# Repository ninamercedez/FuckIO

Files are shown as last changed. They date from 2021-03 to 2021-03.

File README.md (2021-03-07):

# FuckIO
An opensource fucking machine, that is far superiour to anything on the market.
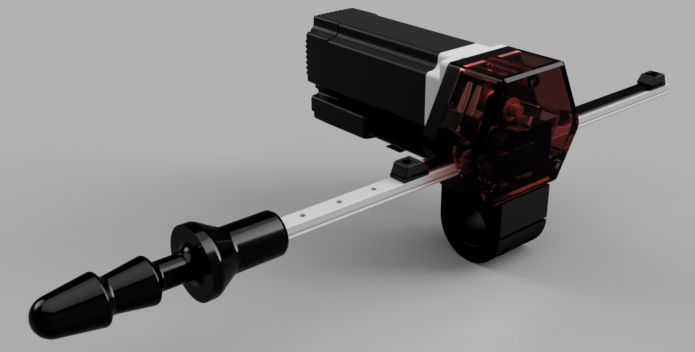
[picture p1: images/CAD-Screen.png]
Rendering


## Specs
* Easy to built just with a 3D-printer, screwdrivers and easy-to-source parts.
* Completely 3D-printable with easy to print parts and almost no supports. Also avoiding tight tolerances to make this accessable as possible. 
* Simple, yet verastile mechanics.
* Based on a linear position drive, not a crank mechanism.
* Double 24V PWM output to drive external systems. Could be lube pumps, vibrators, etc.

## Mechanics
The mechanics is a direct derivative of an other open source project called OSSM. You can also find some informations about this build on their Discord.
https://github.com/KinkyMakers/OSSM-hardware

The motor mount is designed for a NEMA23 servo or stepper motor. Any motor fitting to this standart should work. 

### BOM
* iHSV57-30-18-36-... integrated servo motor from JMC
* 24V Power Brick Mean Well GST280A24-C6P 
* 40cm MGN12H linear rail
* 4x 605-2RS Z2 bearings
* Micro Switch
* GT2 20 Tooth Pulley for 8mm Axis and a 10mm belt
* GT2 belt with 10mm width
* Various M3 and M5 screws and nuts
* Arduino Nano33 IoT

## Electronics
The electronics board is used to interface an external stepper or servo controller. I can't drive a motor directly. It is based around an Arduino Nano33 IoT to enable BLE or WiFi support. It sends 5V DIR, PUL, ENA signals and expects FAULT signal and a homing switch. Two MOSFETs with freewheeling diodes allow PWM control of external systems running of the 24V supply.

## Firmware
The firmware uses a self developed stepper library. It uses the SAMD21 timer perihperials to generate the PUL signal. That way it is possible to create a much higher step rate with no processor loading. Popular Arduino libraries like AccelStepper are not up to the task.

__Do not use this firmware! It is heavly beeing worked on. It will destroy your hardware!__

## Control Software
No control software yet. But it is planned to use node-red in combination with MQTT messages.

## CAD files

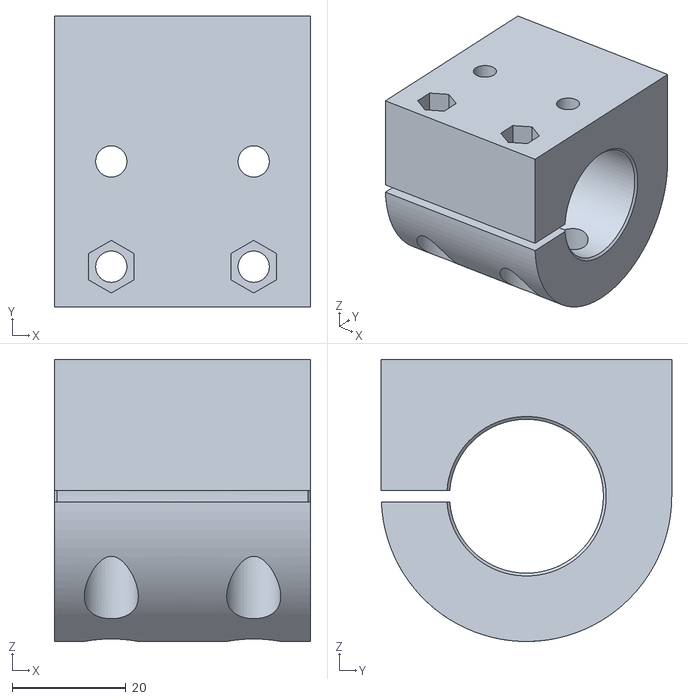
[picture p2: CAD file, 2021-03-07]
hardware/mechanics/3_4in Pipe Clamp.stl
45.0 x 51.0 x 49.5

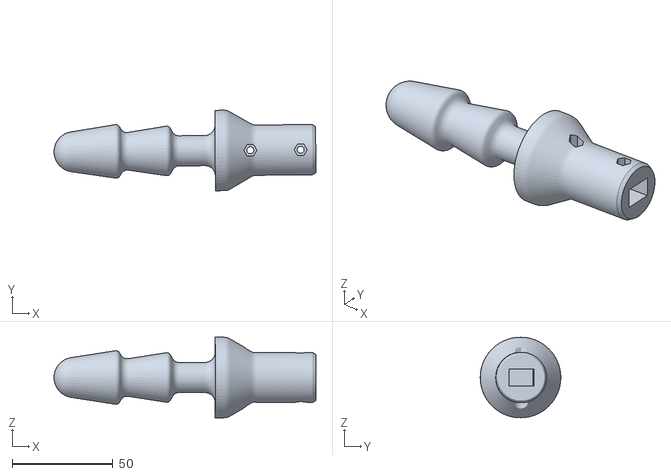
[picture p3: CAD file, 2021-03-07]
hardware/mechanics/Vac-u-Lock.stl
130.1 x 40.0 x 40.0

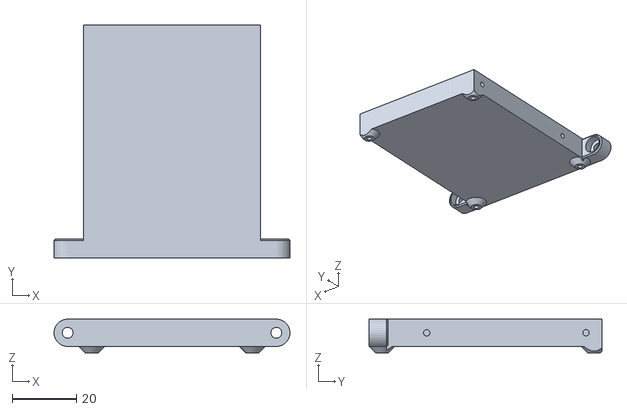
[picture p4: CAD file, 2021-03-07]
hardware/mechanics/PCB Holder.stl
73.5 x 72.6 x 10.5

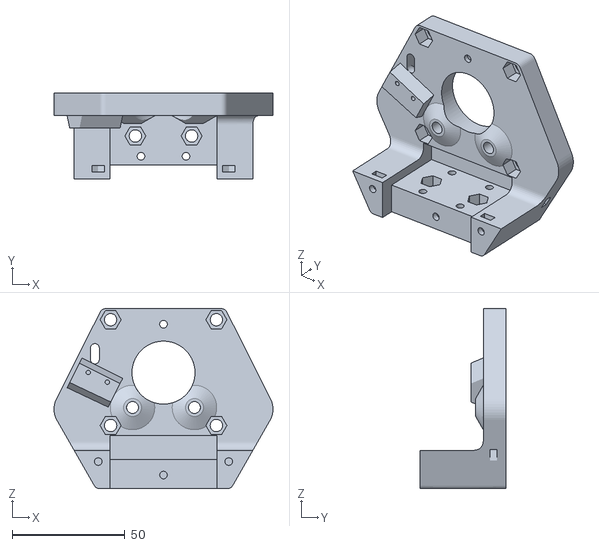
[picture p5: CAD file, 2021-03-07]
hardware/mechanics/Motor Mount.stl
97.3 x 38.0 x 80.0

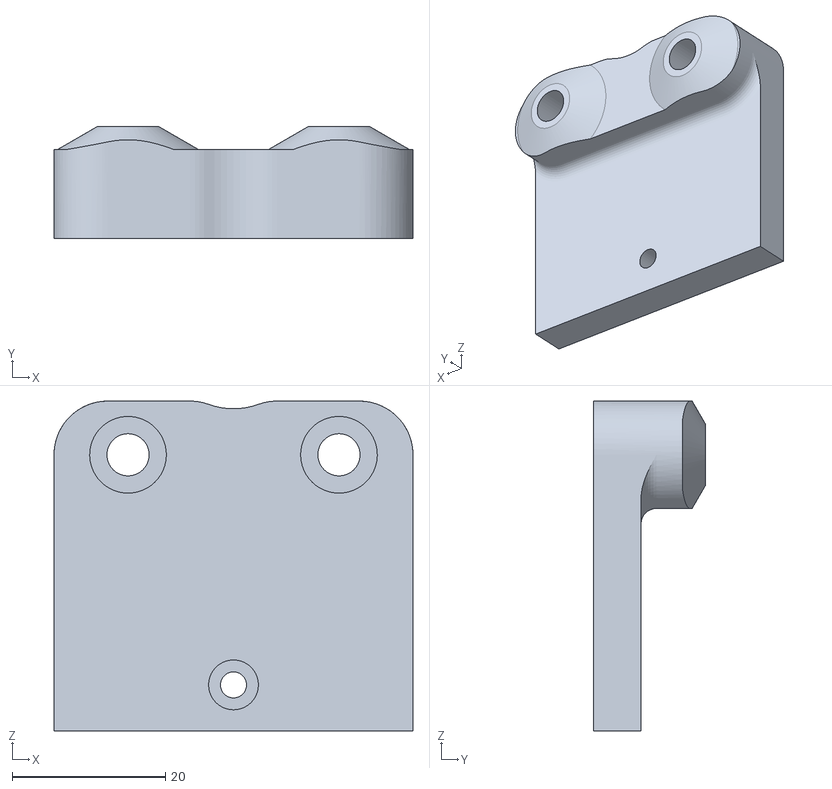
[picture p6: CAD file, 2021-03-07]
hardware/mechanics/Bearing Holder.stl
46.8 x 14.6 x 43.0

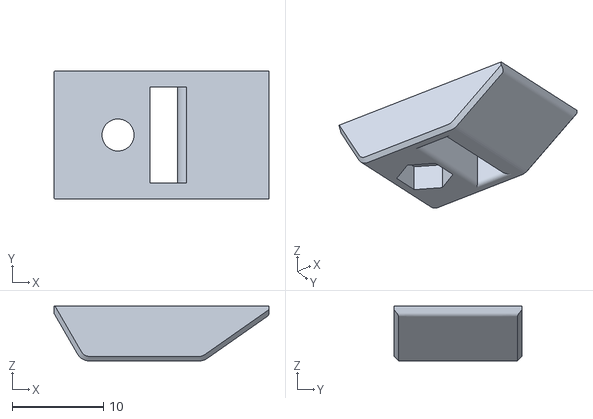
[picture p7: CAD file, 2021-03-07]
hardware/mechanics/Belt Clamp Top.stl
23.5 x 14.0 x 6.00

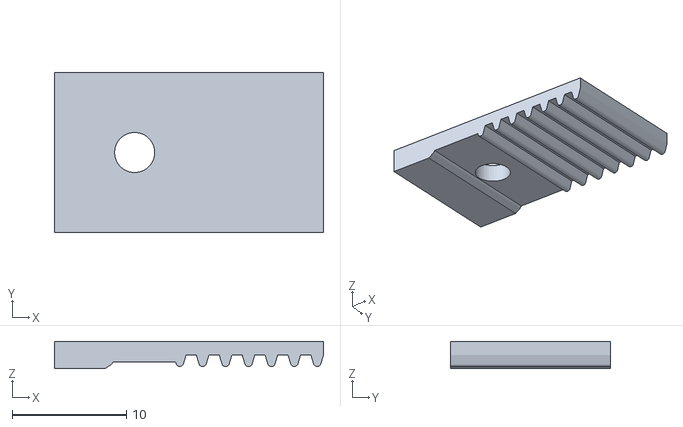
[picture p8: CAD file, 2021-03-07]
hardware/mechanics/Belt Clamp Bottom.stl
23.5 x 14.0 x 2.40

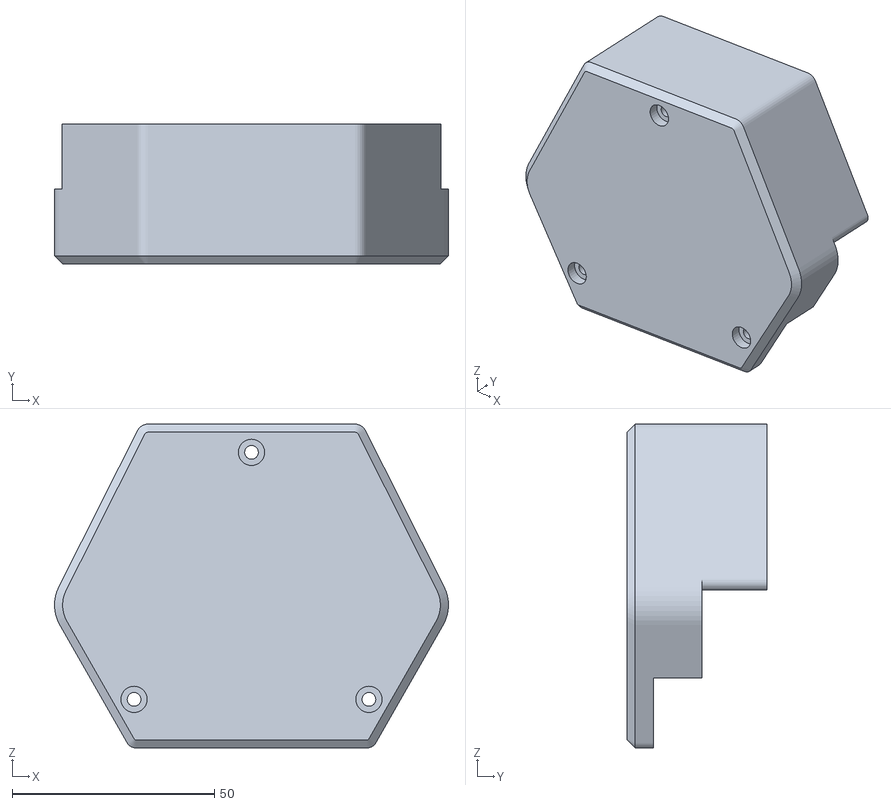
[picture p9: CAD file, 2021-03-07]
hardware/mechanics/Front Cover.stl
97.3 x 34.5 x 80.0

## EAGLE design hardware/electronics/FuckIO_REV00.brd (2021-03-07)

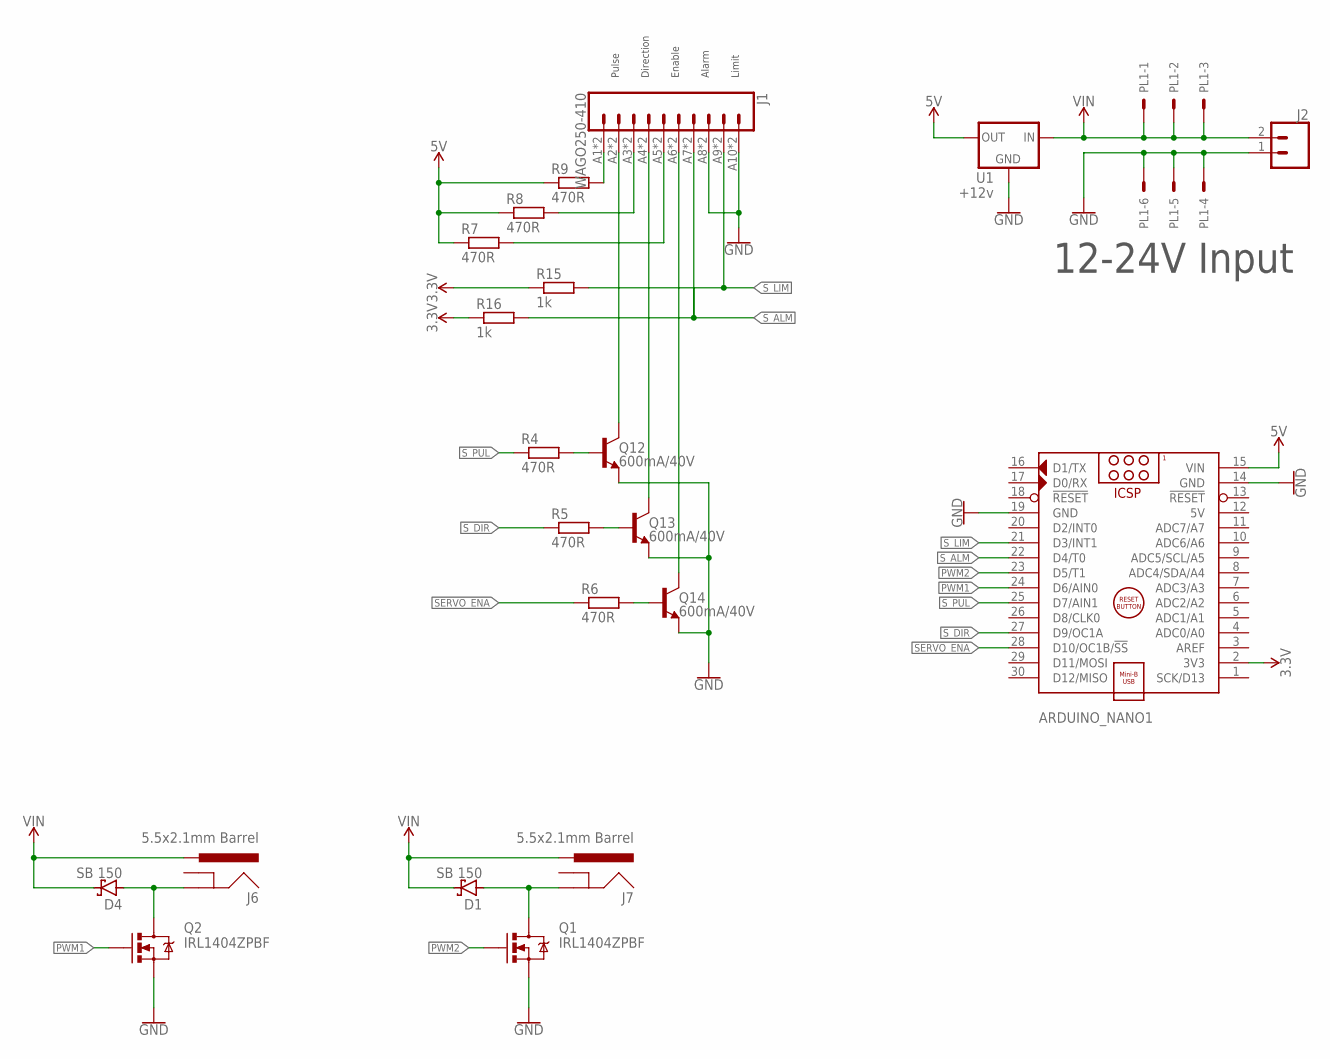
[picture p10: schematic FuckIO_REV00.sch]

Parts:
ARDUINO_NANO1: ARDUINO_NANO; ARDUINONANOV30_ARDUINO_NANO
D1, D4: SB 150; DIODE_DO41-10
J1: WAGO250-410; BEE_WAGO250-410
J2: CONN_025MM; SPARKFUN-CONNECTORS_SCREWTERMINAL-5MM-2
J6, J7: 5.5x2.1mm Barrel; SPARKFUN-CONNECTORS_POWER_JACK_PTH
PL1: CON-MOLEX-2_555X-6H; CON-MOLEX-2_5569-6
Q1, Q2: IRL1404ZPBF; BEE_TO220-IGO
Q12, Q13, Q14: 600mA/40V; SPARKFUN-DISCRETESEMI_TO-92
R4, R5, R6, R7, R8, R9: 470R; RCL_0204/5
R15, R16: 1k; RCL_0204/5
U1: +12v; SPARKFUN-IC-POWER_TO220-IGO

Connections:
3.3V: ARDUINO_NANO1.2 (3V3), R15.1, R16.1
5V: ARDUINO_NANO1.12 (5V), ARDUINO_NANO1.15 (VIN), R7.1, R8.1, R9.1, U1.OUT
GND: ARDUINO_NANO1.14 (GND), ARDUINO_NANO1.19 (GND), J1.A8 (8), J1.A10 (10), J1.B8 (8), J1.B10 (10), J2.1, PL1.4, PL1.5, PL1.6, Q1.S, Q2.S, Q12.3 (E), Q13.3 (E), Q14.3 (E), U1.GND
unnamed: J1.A5 (5), J1.B5 (5), R7.2
unnamed: J1.A3 (3), J1.B3 (3), R8.2
unnamed: J1.A1 (1), J1.B1 (1), R9.2
unnamed: J1.A6 (6), J1.B6 (6), Q14.1 (C)
unnamed: J1.A4 (4), J1.B4 (4), Q13.1 (C)
unnamed: J1.A2 (2), J1.B2 (2), Q12.1 (C)
unnamed: Q12.2 (B), R4.2
unnamed: Q13.2 (B), R5.2
unnamed: Q14.2 (B), R6.2
unnamed: D4.A, J6.GND, Q2.D
unnamed: D1.A, J7.GND, Q1.D
PWM1: ARDUINO_NANO1.24 (D6/AIN0), Q2.G
PWM2: ARDUINO_NANO1.23 (D5/T1), Q1.G
SERVO_ENA: ARDUINO_NANO1.28 (D10/OC1B/!SS), R6.1
S_ALM: ARDUINO_NANO1.22 (D4/T0), J1.A7 (7), J1.B7 (7), R16.2
S_DIR: ARDUINO_NANO1.27 (D9/OC1A), R5.1
S_LIM: ARDUINO_NANO1.21 (D3/INT1), J1.A9 (9), J1.B9 (9), R15.2
S_PUL: ARDUINO_NANO1.25 (D7/AIN1), R4.1
VIN: D1.C, D4.C, J2.2, J6.PWR, J7.PWR, PL1.1, PL1.2, PL1.3, U1.IN

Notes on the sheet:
Pulse
Direction
Enable
Alarm
12-24V Input
Limit

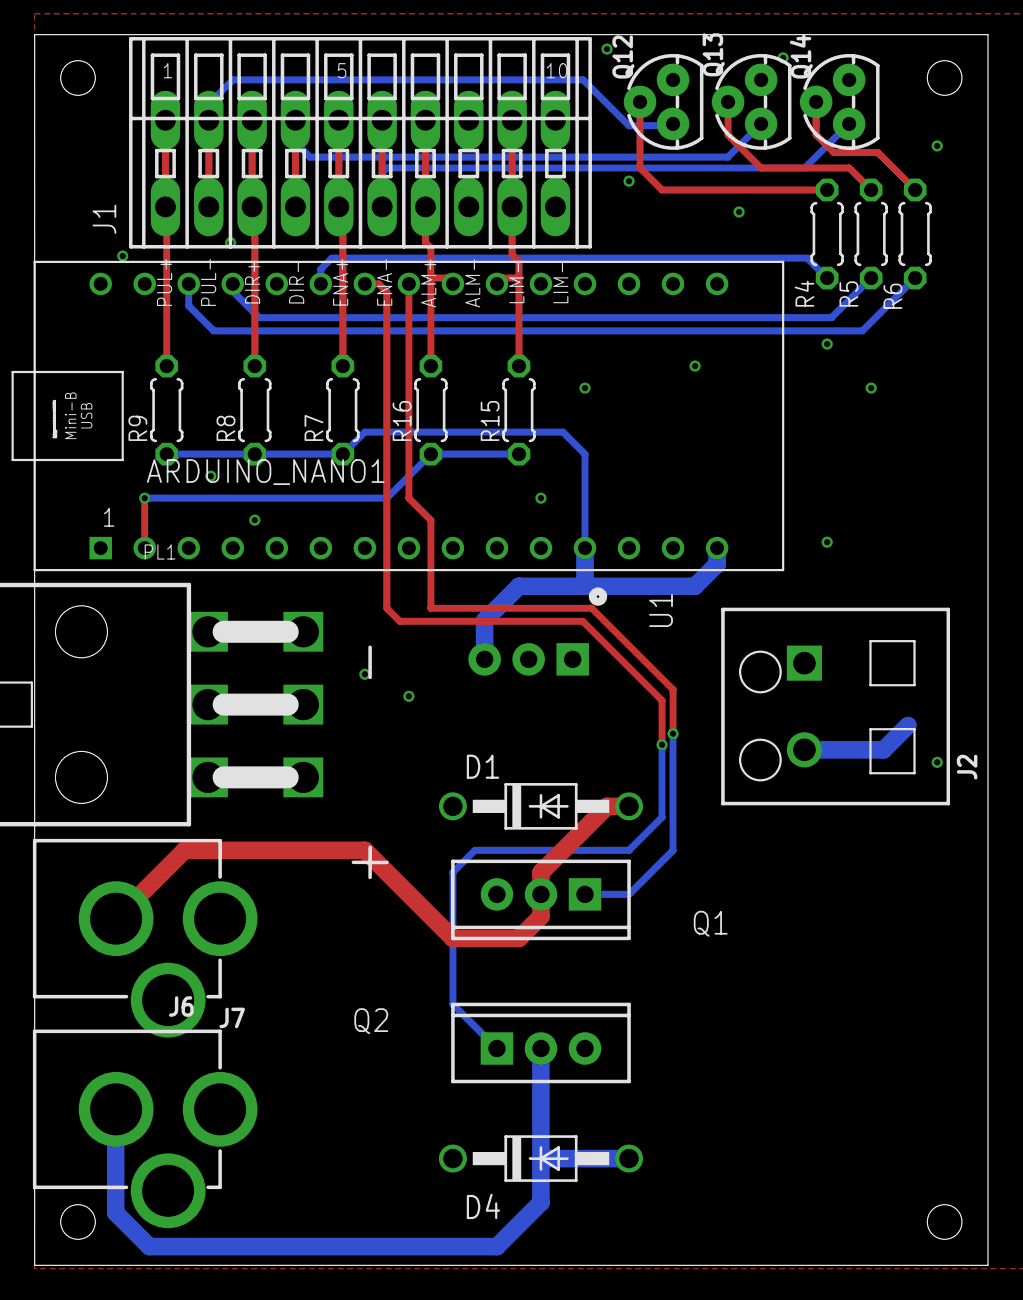
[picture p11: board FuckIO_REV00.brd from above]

Board: 2 copper layers, 55.0 x 71.0 mm, 22 parts (0 on the bottom side), 22 nets.

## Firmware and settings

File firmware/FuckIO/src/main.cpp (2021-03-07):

#include <Arduino.h>
#include <SPI.h>
#include <WiFiNINA.h>
#include <MQTT.h>
#include <SAMD21Step.h> 
#include <MotionCtrl.h>



// Pin Definitions
const int S_PUL = 11;
const int SE_PUL = 7;
const int S_DIR = 9;
const int SE_DIR = A2;
const int SERVO_ENA = 10;
const int S_LIM = 3;
const int SE_LIM = A7;
const int S_ALM = 4;
const int SE_ALM = A1;

const int PWM1 = 6;
const int PWM2 = 5;

// Servo Settings:
#define STEP_PER_REV      3200   // How many steps per revolution of the motor (S1 on)
#define PULLEY_TEETH      15     // How many teeth has the pulley
#define BELT_PITCH        3      // What is the timing belt pitch in mm
#define MAX_TRAVEL        200    // What is the maximum physical travel in mm
#define KEEPOUT_BOUNDARY  5      // Soft endstop preventing hard crashes in mm. Will be 
                                 // subtracted twice from MAX_TRAVEL
#define MAX_RPM           2900   // What is the maximum RPM of the servo
#define MAX_ACC           30000  // Maximum acceleration in mm/s^2
#define INVERSE           false  // Set to true to invert the direction signal
                                 // The firmware expects the home switch to be located at the 
                                 // end of an retraction move. That way the machine homes 
                                 // itself away from the body.

// Derived Servo Settings
#define STEP_PER_MM       STEP_PER_REV / (PULLEY_TEETH * BELT_PITCH)
#define TRAVEL            MAX_TRAVEL - (2 * KEEPOUT_BOUNDARY)
#define MIN_STEP          int(0.5 + KEEPOUT_BOUNDARY * STEP_PER_MM)
#define MAX_STEP          int(0.5 + (MAX_TRAVEL - KEEPOUT_BOUNDARY) * STEP_PER_MM)
#define MAX_STEP_PER_SEC  int(0.5 + (MAX_RPM * STEP_PER_REV) / 60)
#define MAX_STEP_ACC      int(0.5 + MAX_ACC * STEP_PER_MM)

// Coniguration of the stepper motor
StepperConfig stepper0config = {
  .pulsePin = S_PUL,                   // Arduino pin number for the pulse pin. Must be a pin with a TCC timer output (see PinLookup). One timer can exclusivly serve only one pin.
  .dirPin = S_DIR,                     // Arduino pin number of the direction signal. May be any pin.
  .enablePin = SERVO_ENA,              // Arduino pin number of the driver enable signal. May be any pin. Set to -1 if not used.
  .enableActiveLow = true,             // Set to true if the enable signal is active low. For active high set to false.
  .alarmPin = S_ALM,                   // Arduino pin number of the driver alarm signal. Must be an interrupt pin. Set to -1 if not used.
  .alarmActiveHigh = true,             // Set to true if the alarm signal is active high. For active low set to false.
  .homePin = S_LIM,                    // Arduino pin number of the home switch. Must be an interrupt pin. Homing is mandatory
  .homeActiveHigh = true,              // Set to true if the home signal is active high. For active low set to false.
  .invertPulse = true,                 // Set to true if you need an active low pulse signal
  .minPulseWidth = 4.0,                // Minimum pulse width in µs
  .maxVelocity = MAX_STEP_PER_SEC,     // Maximum velocity in steps/sec
  .maxAcceleration = MAX_STEP_ACC,     // Maximum accelceration & decceleratin in steps/sec^2
  .minPosition = MIN_STEP,             // Minimum position of the axis in steps
  .maxPosition = MAX_STEP,             // Maximum position of the axis in steps
  .homePosition = 0,                   // The position of home. When the home switch is triggered position will be set to this value. May be outside the minPosition and maxPosition boundary
  .invertDirection = false,            // Set to true to invert the movement direction
  .invertHoming = false                // Set to true to invert the direction for searching the home switch
};

// timer tester
Stepper stepper0;
MotionCtrl& motion = MotionCtrl::instance();

void setup() {
  pinMode(LED_BUILTIN, OUTPUT);

  Serial.begin(115200);
  while (!Serial) {
    delay(10);
  }
  
  Serial.println("Timer callback tester");

  stepper0.begin(&stepper0config);
  motion.begin(5.0, &stepper0);
  
  stepper0.enableDriver(true);
}

void loop() {

}





/*
WiFiClient net;
MQTTClient client(128); //The passed value denotes the read and write buffer size.

char ssid[] = "Kellerkind";
char pass[] = "Putzplan"; 
byte mac[6]; // the MAC address of your Wifi shield

char host[] = "192.168.1.24"; // Note: Local domain names (e.g. "Computer.local" on OSX) are not supported by Arduino. You need to set the IP address directly.
char user[] = "";
char pwd[] = "";
char clientID[] = "FuckIO"; //MQTT ClientID
char topic[] = "FuckIO/control/+";

unsigned int currentMillis = 0;
unsigned int startMillis = 0;
unsigned int microsPulses = 125;

void messageReceived(String &topic, String &payload) { 
bool bvalue = false;
  Serial.println("Message: " + topic + " - " + payload);
  if (topic.startsWith("FuckIO/control")) {
    topic.remove(0, topic.lastIndexOf('/') + 1);
    if (topic.equals("run")) {
      bvalue = payload.equalsIgnoreCase("TRUE");
      digitalWrite(SERVO_ENA, bvalue);  // Enable or disable the servo motors
      digitalWrite(LED_BUILTIN, bvalue);  // Enable or disable the servo motors
      // Handle Timer
    }
    if (topic.equals("rpm")) {
      microsPulses = int((1.0/((payload.toInt() / 60.0)*8000))*1000000);
      Serial.println(microsPulses);
    }
    if (topic.equals("dir")) {
      bvalue = payload.equalsIgnoreCase("TRUE");
      digitalWrite(S_DIR, bvalue);  // CW / CWW rotation
      digitalWrite(SE_DIR, bvalue);  // CW / CWW rotation
    }
    if (topic.equals("pwm")) {
      analogWrite(PWM1, constrain(payload.toInt(), 0, 255));
      analogWrite(PWM2, constrain(payload.toInt(), 0, 255));
    }
  }
}

void connect() {
  String macAdress = "";

  WiFi.begin(ssid, pass);

  Serial.print("connecting WiFi ");
  while (WiFi.status() != WL_CONNECTED) {
    Serial.print(".");
    delay(500);
  }

  // print the SSID of the network you're attached to:
  Serial.print("\nSSID: ");
  Serial.println(WiFi.SSID());

  // print your WiFi shield's IP address:
  IPAddress ip = WiFi.localIP();
  Serial.print("IP Address: ");
  Serial.println(ip);

  // print your MAC address:
  WiFi.macAddress(mac);
  Serial.print("MAC Address: ");
  Serial.print(mac[5],HEX);
  Serial.print(":");
  Serial.print(mac[4],HEX);
  Serial.print(":");
  Serial.print(mac[3],HEX);
  Serial.print(":");
  Serial.print(mac[2],HEX);
  Serial.print(":");
  Serial.print(mac[1],HEX);
  Serial.print(":");
  Serial.println(mac[0],HEX);

  // print the received signal strength:
  long rssi = WiFi.RSSI();
  Serial.print("signal strength (RSSI): ");
  Serial.print(rssi);
  Serial.println(" dBm");

  client.begin(host, net);

  Serial.print("connecting to MQTT-Server " + String(host));
  while (client.connect(clientID, user, pwd) == false) {
    Serial.print("*");
    delay(500);
  }

  Serial.println("\nsubscribing to " + String(topic));
  client.onMessage(messageReceived);
  if (client.subscribe(topic))
  {
    Serial.println("Success");
  } else
  {
    Serial.println("\nCouldn't subscribe");
  } 

  client.publish("/hello", "world");

}

void setup() {

  // Initialize Pins
  pinMode(S_PUL, OUTPUT);
  pinMode(SE_PUL, OUTPUT);
  pinMode(S_DIR, OUTPUT);
  pinMode(SE_DIR, OUTPUT);
  digitalWrite(S_DIR, HIGH);
  digitalWrite(SE_DIR, HIGH);
  pinMode(SERVO_ENA, OUTPUT);
  digitalWrite(SERVO_ENA, LOW);  //Disarm the servo motors
  pinMode(S_LIM, INPUT);
  pinMode(SE_LIM, INPUT);
  pinMode(S_ALM, INPUT);
  pinMode(SE_ALM, INPUT);
  pinMode(PWM1, OUTPUT);
  pinMode(PWM2, OUTPUT);
  pinMode(LED_BUILTIN, OUTPUT);
  digitalWrite(LED_BUILTIN, HIGH);

  Serial.begin(115200);
  connect();
}

void loop() {
    
  currentMillis = millis();
  
  if (currentMillis - startMillis >= 100) {
    startMillis = currentMillis;
    client.loop();
    Serial.println("signal strength (RSSI): " + WiFi.RSSI());

    if (!client.connected()) {
      Serial.println("Lost connection! Try to reconnect.");
      connect();
    }
  }

  digitalWrite(S_PUL, HIGH);
  digitalWrite(SE_PUL, HIGH);
  delayMicroseconds(microsPulses);
  digitalWrite(S_PUL, LOW);
  digitalWrite(SE_PUL, LOW);
  delayMicroseconds(microsPulses);

}
*/
